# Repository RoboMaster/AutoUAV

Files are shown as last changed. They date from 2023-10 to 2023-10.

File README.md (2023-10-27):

# Robomaster自主无人机

## 注意
组装文档中采用了悬挂方案安装飞控，该方案能够极大地减小震动对imu的影响。但是长时间的拉伸会使得皮筋产生脆化而失去弹性。将皮筋更换为工业橡皮筋可缓解该问题。同时碳纤维板上预留了飞控安装孔位，也可以选择直接将飞控安装到碳板上，但是该做法的imu减震性能不佳。

## 简介
为了降低选手参与自主无人机赛事的门槛，减少用于调试安装设备的精力，推出了基于DJI Avata平台，Nvidia Jetson Xiaver NX 和 Ardupilot的开源自主无人机方案。  
*docs/RMUA2023自主无人机开源手册_bom.xlsx*包含有所需设备的详细信息，根据这个表格可以获得所需的所有零部件。  
*docs/RMUA2023自主无人机开源手册.md*详细介绍了安装，调试，参数配置，程序开发的全过程。按照该手册的指引，能够从0开始获得可以自主定位，手动或者离线控制的自主无人机。    
*models*中包含有所需的非标件模型文件。   
*catkin_ws_d430_ros*含有多个基本离线控制程序案例以供参考：
1. 视觉定位 (*catkin_ws_d430_ros/src/d430_slam*)；
2. 定点悬浮 (*catkin_ws_d430_ros/src/offboard*)；
3. 位置控制巡航 (*catkin_ws_d430_ros/src/offboard*)；
4. 速度控制巡航 (*catkin_ws_d430_ros/src/offboard*)；

## License
本项目使用*GNU GPLv3*，查看*LICENSE*文件获得更多信息。

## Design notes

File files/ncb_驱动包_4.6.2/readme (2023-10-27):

### NCB00 USB-OTG and TF socket driver setup

## FOR EMMC NX module
	// ON PC
	1, cp tegra194-p3668-all-p3509-0000-ncb.dtb ~/nvidia/nvidia_sdk/JetPack_4.6_Linux_JETSON_XAVIER_NX_TARGETS/Linux_for_Tegra/kernel/dtb/tegra194-p3668-all-p3509-0000.dtb
	2, Let NX/NANO enter recovery mode and connect to PC via micro-USB
	3, cd ~/nvidia/nvidia_sdk/JetPack_4.6_Linux_JETSON_XAVIER_NX_TARGETS/Linux_for_Tegra
	4, sudo ./flash.sh -r -k kernel-dtb p3449-0000+p3668-0001-qspi-emmc mmcblk0p1
	5, wait NX/NANO booting up.  

	// On NX
	1, cp extlinux.conf /boot/extlinux/ 
	2, reboot //important!!!

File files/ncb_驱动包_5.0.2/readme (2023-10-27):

### NCB00 USB-OTG and TF socket driver setup

## FOR EMMC NX module
	// ON NX
	1, sudo cp kernel_tegra194-p3668-0001-ncb00.dtb* /boot/dtb/
	2, sudo cp extlinux.conf /boot/extlinux/ 
	3, sudo reboot //important!!!
## USE TF card of NCB as rootfs
   1, Edit extlinux.conf to switch emmc and tf as rootfs  // ON emmc 
   2, ON TF card: cp extlinux-tf.conf /boot/extlinux/extlinux.conf //

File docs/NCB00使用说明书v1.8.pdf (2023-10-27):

未经同意，请勿转载全部或部分内容！

第 1 页 共 19 页

# NCB00 说明书

### 版本：v1.8

第 2 页 共 19 页

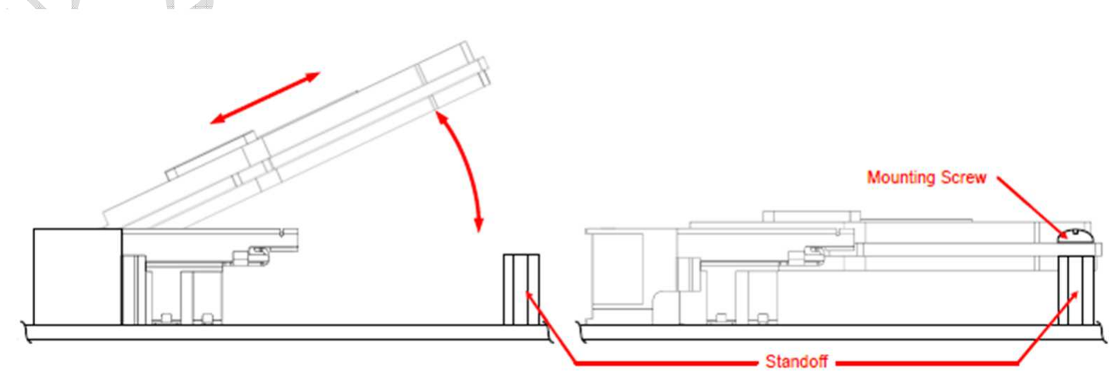
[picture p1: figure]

第 3 页 共 19 页

# 1. 版本历史

版本 | 修改说明 | 作者 | 备注
1.8 | 增加常见问题 | 张建军
1.7 | 完善 CSI 接口 I2C 说明，增加 USB2.0 说明 | 张建军
1.6 | 增加常见问题、IMU 等 | 张建军
1.5 | 针对 B07 更新 SPI 引脚定义说明 | 张建军
1.4 | 修正 NX GPIO 编号定义 | 张建军
1.3 | 添加 B05 版本说明 | 张建军
1.2 | 添加 B04 版本说明 | 张建军
1.1 | 添加 B03A 版本说明 | 张建军
1.0 | 新建 | 张建军

# 2. 安装方法

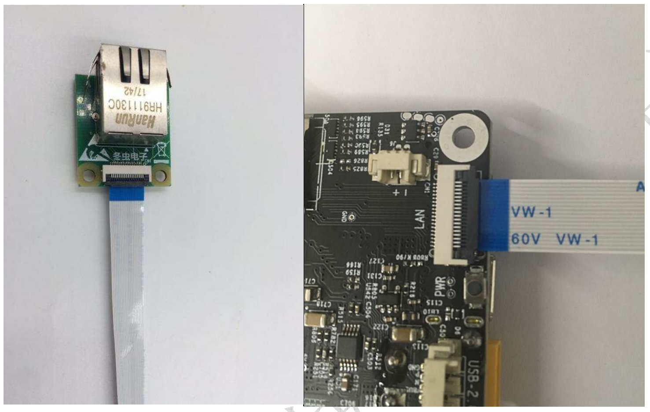
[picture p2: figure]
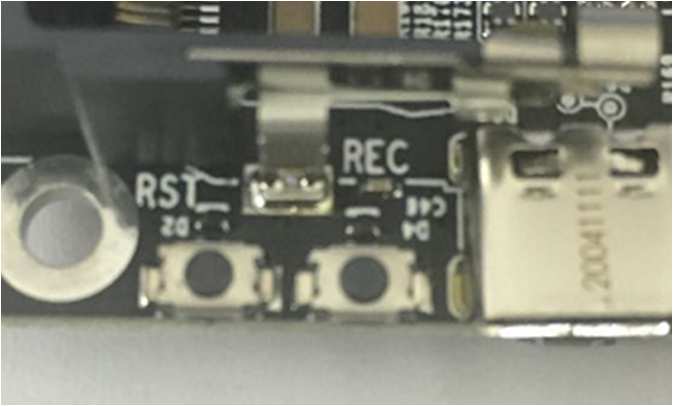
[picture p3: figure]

第 4 页 共 19 页

# 3. 配件连接

虽然板上配件接口大部分采用防呆防接反设计，但在连接时也必须在断电状态下进行， 并确认配件接到了相应的接口。
除特别说明外，配件的 FPC 接口连接方式都是相同的，均采用下接方式。如网口板的连 接照片

# 4. 如何刷机

1，刷机准备：准备一台 ubuntu18.04 以上系统的 PC，并安装 NVIDIA 最新版本的 sdkmanager。
2，进入 Recovery 模式：按住 REC（recovery）键，再按一下 RST（Reset）键，约 2 秒后 松开 REC 键，NANO/NX 进入 Recovery 模式，等待刷机。
3，刷机：通过 MicroUSB 线连接到 PC，并启动 sdkmanager，按提示步骤完成刷机。

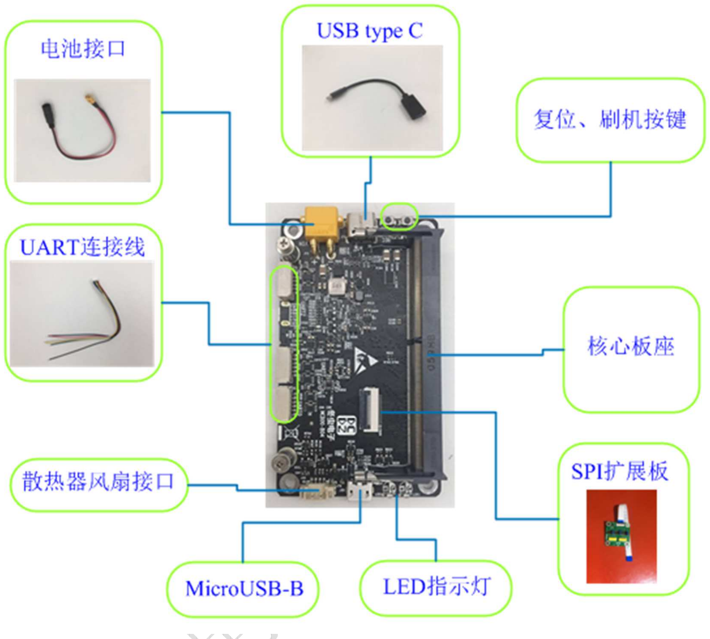
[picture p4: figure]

第 5 页 共 19 页

# 5. 接口说明

顶面视图

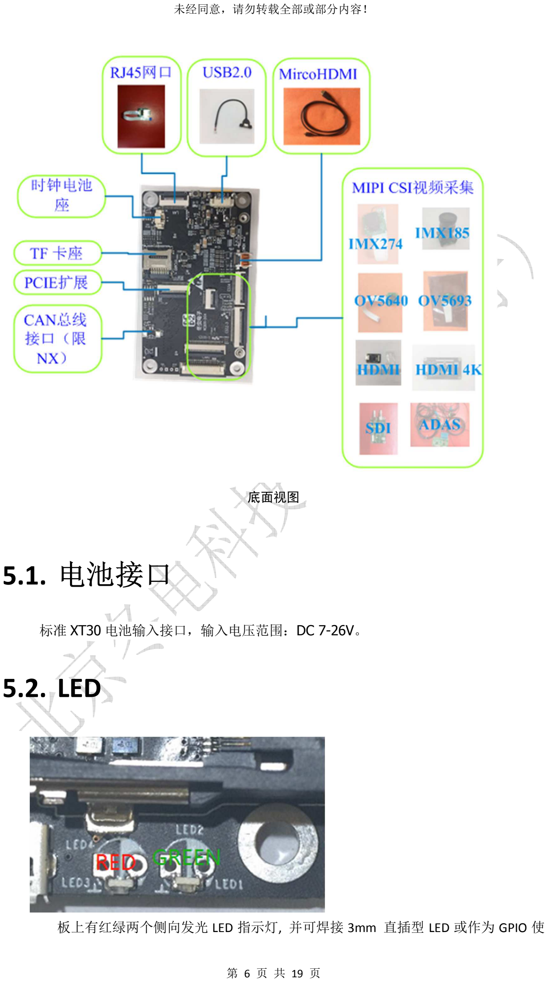
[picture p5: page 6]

第 6 页 共 19 页

底面视图

# 5.1. 电池接口

标准 XT30 电池输入接口，输入电压范围：DC 7-26V。

# 5.2. LED

板上有红绿两个侧向发光 LED 指示灯, 并可焊接 3mm 直插型 LED 或作为 GPIO 使

第 7 页 共 19 页

用。红色为底板电源指示灯，绿色为软件可控制的。
绿色 LED 控制信号为 GPIO12（开发板上的定义)，高电平时点亮。NANO 系统中对 应 GPIO 号为 194，NX 中为 268
Linux 系统中 IO 命令行调用方法：

echo "<number>" > /sys/class/gpio/export
echo "out" > /sys/class/gpio/gpio<number>/direction echo "0" > /sys/class/gpio/gpio<number>/value echo "1" > /sys/class/gpio/gpio<number>/value

# 5.3. MicroHDMI

HDMI type D 母座，HDMI 显示输出接口

# 5.4. UART0,UART1,UART2

UART0~1 为 4 线制 UART 接口，UART2 为 2 线制, 可把 UART 信号线配置为 GPIO 使用（需要修改驱动）。信号电平可选择为 5V 或 3.3V，出厂缺省为 3.3V 电平，采用 6pin 1.25mm 间距 GH1.25 带锁扣连接器。拔出时注意要按压解锁按钮。 UART0~UART2 与系统中对应关系如下表所示
UARTX | NANO | NX | 备注
UART0 | /dev/ ttyTHS2 | /dev/ ttyTHS1
UART1 | /dev/ ttyTHS1 | /dev/ ttyTHS0 | 系统占用（note）
UART2 | /dev/ttyS0 | /dev/ttyTCU0 | 系统占用（note）

note：在 NVIDIA 的官方系统中 UART1 和 UART2 默认为系统控制台，可按下面方法修 改为普通 UART 使用
UART1: 修改方法

### $ systemctl stop nvgetty $ systemctl disable nvgetty $ udevadm trigger $ sudo reboot UART2: 去除 cbootargs 和 extlinux.conf 中使用 ttyS0 的项

引脚定义如下图所示

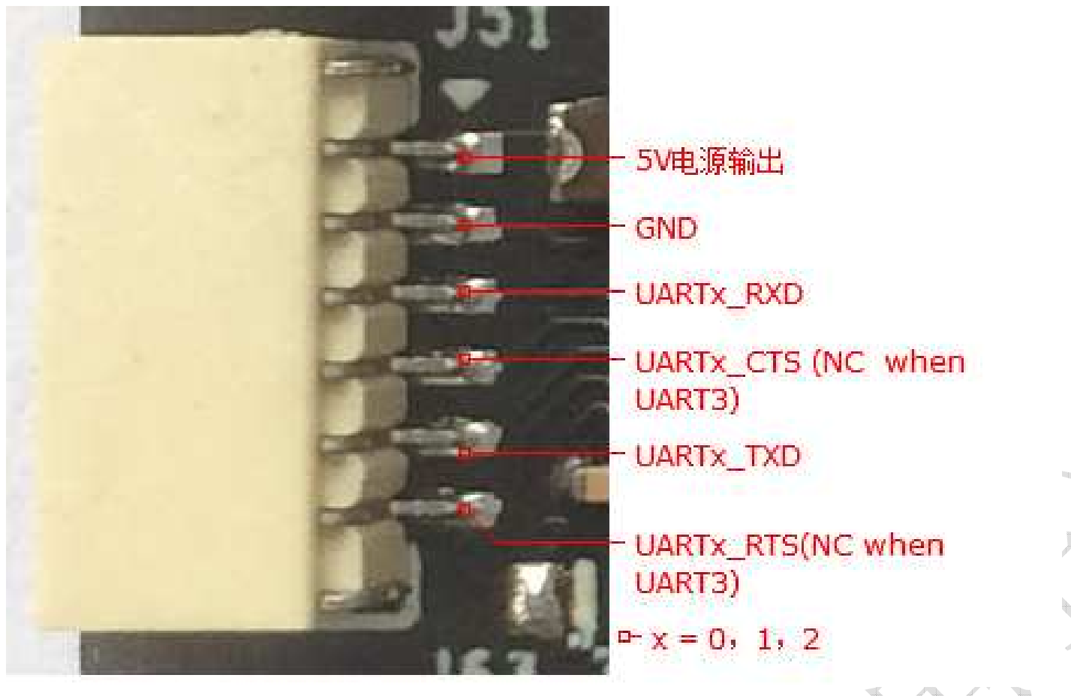
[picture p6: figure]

第 8 页 共 19 页

# 5.4.1. UART0

信号电平可通过接口附近的 R679 和 R678 进行选择，焊接 R679 时为 5V，焊接 R678 时为 3.3V，

# 5.4.2. UART1

信号电平可通过正面的 R681 和 R680 进行选择，焊接 R681 时为 5V，焊接 R680 时为 3.3V，

# 5.4.3. UART2

信号电平可通过正面的 R683 和 R682 进行选择，焊接 R683 时为 5V，焊接 R682 时为 3.3V，

# 5.5. IMU

板载 BMI160 IMU（可选项）, 地址为 7h69。使用 NANO 时 I2C 总线为 I2C1,测试命令： sudo i2cdetect –y –r 1；使用 NX 时 I2C 总线为 I2C8,测试命令：sudo i2cdetect –y –r 8

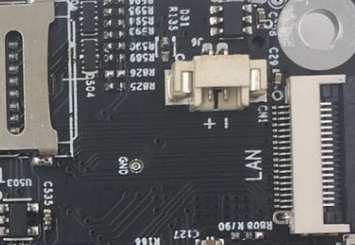
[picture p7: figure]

第 9 页 共 19 页

# 5.6. RTC 后备电池接口

采用 2pin MX1.25mm 座，官方系统默认支持 3V 的充电电池

# 5.7. Fan

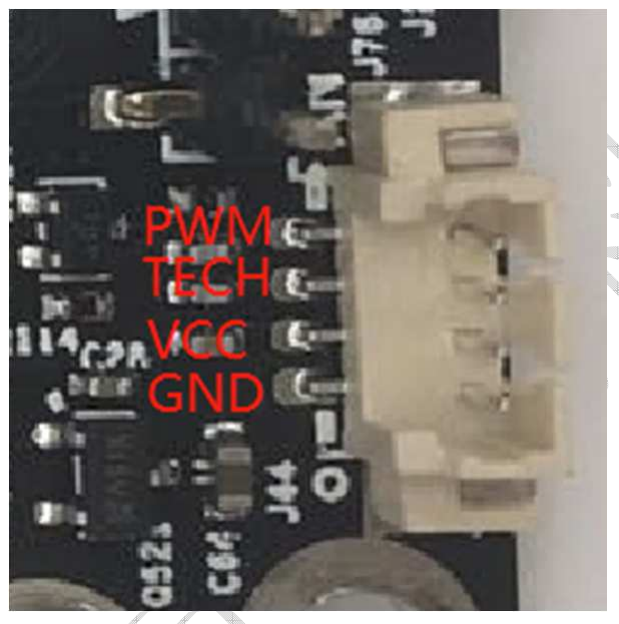
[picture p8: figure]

4pin MX1.25mm 连接器. 测试方法：
：sudo su
：echo 255 > /sys/devices/pwm-fan/target_pwm | //让风扇工作在最高速度

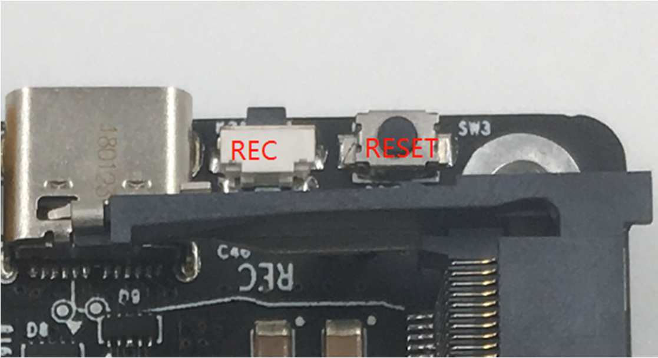
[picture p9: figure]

第 10 页 共 19 页

# 5.8. Key

电源开关键位于 USB type C 背面，其中 Recovery 键为侧向按键。默认为上电开机， 长按电源键超过 10 秒强制关机

# 5.9. USB 2.0 主机接口

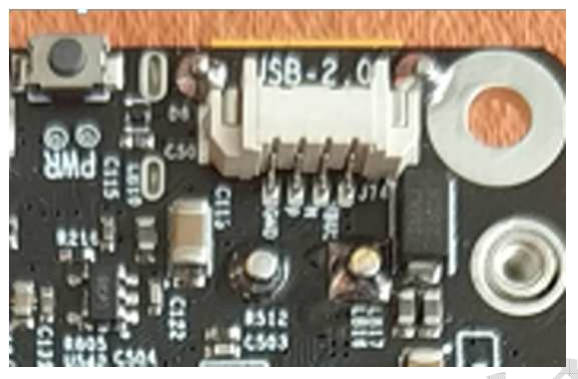
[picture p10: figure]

板载一个 USB2.0 主机接口，采用 4pin MX1.25mm 连接器

# 5.10. Micro USB

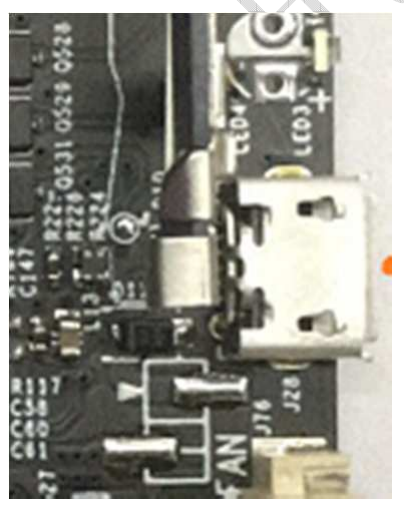
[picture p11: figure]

Micro USB B 座，支持 USB-0TG 功能（B05 以上版本），需要按驱动包中 readme 说明 更新 dtb 激活该功能

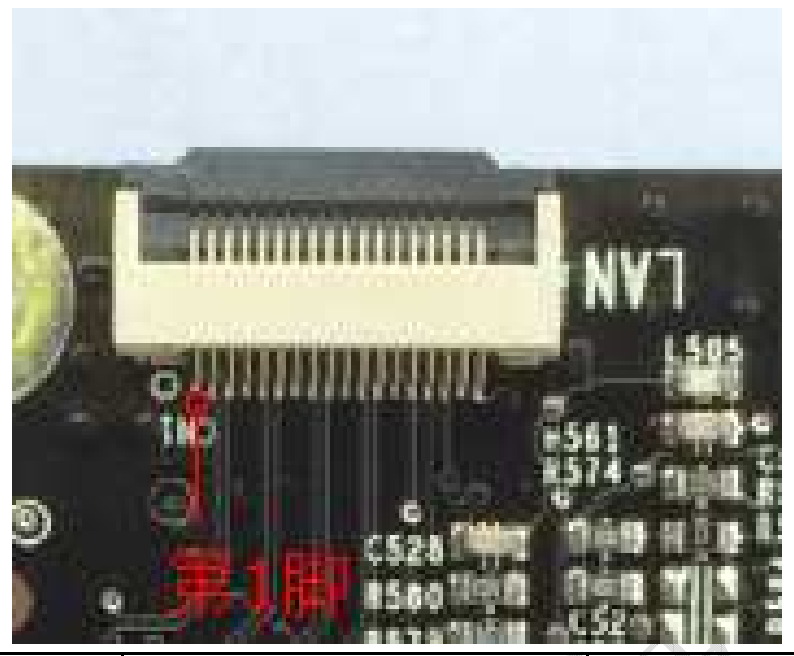
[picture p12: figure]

第 11 页 共 19 页

# 5.11. USB type C 座

标准 USB 3.0 是组合了 USB2.0 信号和 USB3.0 信号的接口，因为技术原因，在使用 USB2.0 设备时可支持任意方向插入，在使用 USB3.0 设备时请注意方向。USB 口电源 默认跟随 3.3V 电源打开，需要使用 GPIO 控制 USB 电源的请联系我司技术人员。

# 5.12. Gbe ethernet

千兆以太网扩展口,采用 18pin 0.5mm FFC 连接器。引脚定义如下所示

引号序号 | 信号名称 | 备注

1 GND
2 GBE_MDI0_N
3 GPE_MDI0_P
4 GND
5 GBE_MDI1_N
6 GBE_MDI1_P
7 GND
8 GBE_MDI2_N
9 GBE_MDI2_P
10 GND
11 GBE_MDI3_N
12 GBE_MDI3_P
13 GND
14 GBE_LED1
15 GBE_LED0
16 GBE_LED2
17 GND
18 | 3V3_SLP | 3.3V 电源输出

第 12 页 共 19 页

# 5.13. GPIO

提供 3 个输入和 3 个输出 IO，，分别位于 3 个 UART 接口。电平 3.3V 或 5V 可选，见 UART 接口电平配置方法，默认电平为 3.3V
系统 IO 编号见下表
UART 接口 | UART 引脚号 | 模组引脚名 | Jetson.GPI O 库 | NANO 系统 IO 号 | NX 系统 IO 号 | 备注
UART0 | 4 | UART0_CTS | -- | 28 | 479 | 输入
| 6 | UART0_RTS | -- | 27 | 478 | 输出
UART1 | 4 | UART1_CTS | 36 | 51 | 429 | 输入
| 6 | UART1_RTS | 11 | 50 | 428 | 输出
UART2 | 4 | GPIO11 | 31 | 200 | 422 | 输入
| 6 | GPIO07 | 32 | 168 | 424 | 输出

注：除了这几个 GPIO 外，LED 控制脚也可配置为 GPIO 使用。

# 5.14. Micro SD

翻盖式 Micro SD 卡座，需要按驱动包中 readme 说明更新 dtb 激活该功能。

# 5.15. EEPROM

板载 2k bit EEPROM, 地址为 7h57。使用 NANO 时 I2C 总线为 I2C2,测试命令：sudo i2cdetect –y –r 2；使用 NX 时 I2C 总线为 I2C0,测试命令：sudo i2cdetect –y –r 0

# 5.16. PCIe 扩展座

引出 PCIe x 1 接口，采用 22pin 0.5mm FFC 连接器，用来连接 miniPCIe 和 M.2 扩展板， 引脚定义如下图所示。

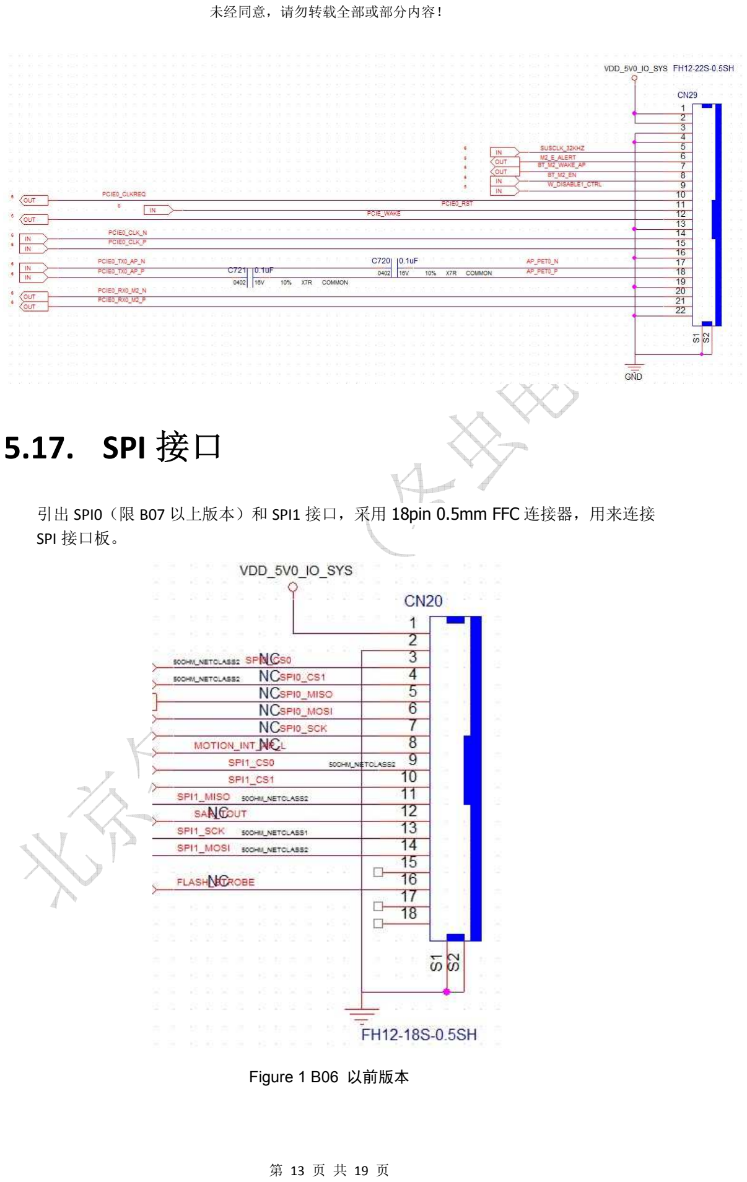
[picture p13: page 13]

第 13 页 共 19 页

# 5.17. SPI 接口

引出 SPI0（限 B07 以上版本）和 SPI1 接口，采用 18pin 0.5mm FFC 连接器，用来连接 SPI 接口板。

Figure 1 B06 以前版本

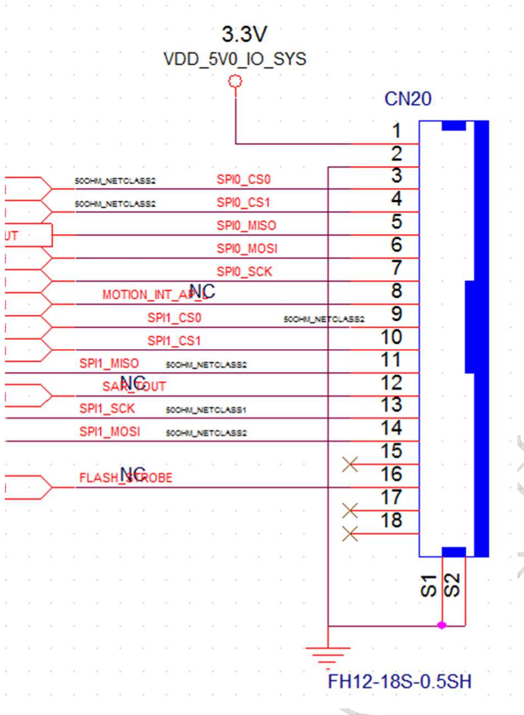
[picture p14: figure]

第 14 页 共 19 页

Figure 2 B07 以后版本

# 5.18. CSI-XX：

核心板的 CSI 信号分成 3 组引出，采用 30pin 和 22pin 0.5mm FFC 连接器。 CSI 接口 I2C 资源分配表
CSI 接口 | NANO | NX
I2C 总线地址 | I2C 设备节点 | I2C 总线地址 | I2C 设备节点
CAM0 | 0x546C0000 | /dev/i2c-6 | 0x3180000 | /dev/i2c-2
CSI0-1 | 同上 | 同上 | 同上 | 同上
CSI2-3 | 0x7000C400 | /dev/i2c-1 | 0x31e0000 | /dev/i2c-8
CSI4 | 0x7000C000 | /dev/i2c-0 | 0xc240000 | /dev/i2c-1

引脚定义如下所示

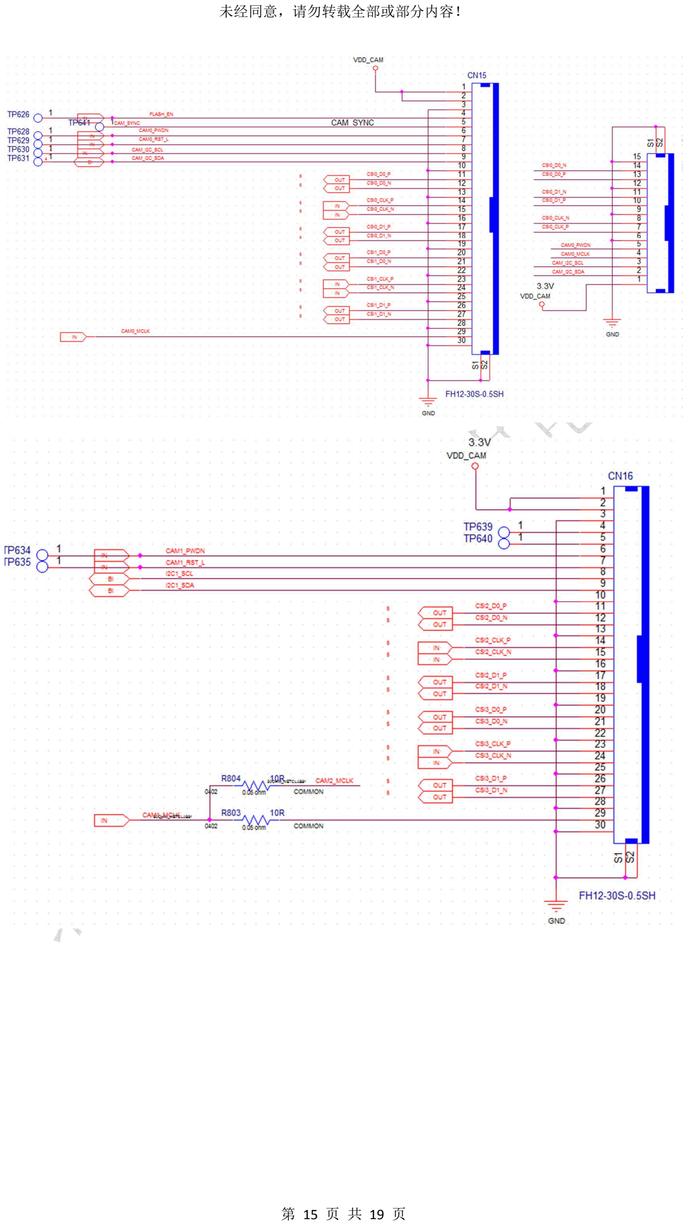
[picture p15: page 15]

第 15 页 共 19 页

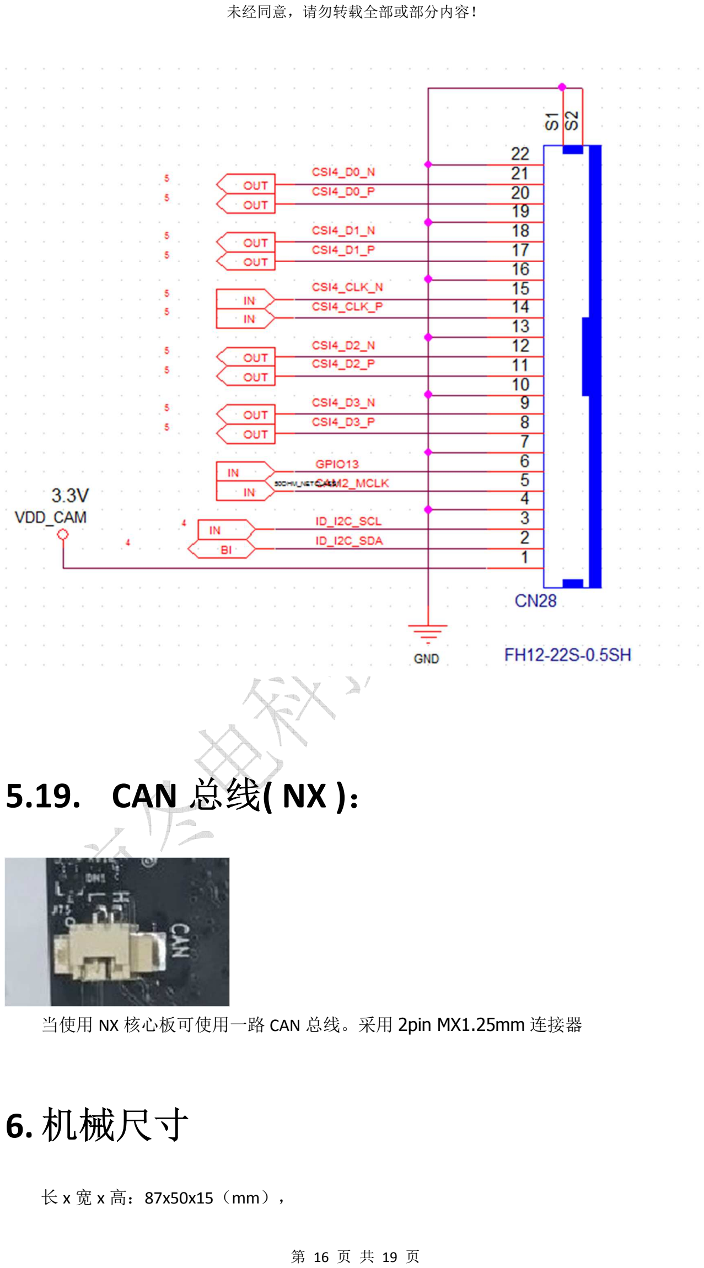
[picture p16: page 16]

第 16 页 共 19 页

# 5.19. CAN 总线( NX )：

当使用 NX 核心板可使用一路 CAN 总线。采用 2pin MX1.25mm 连接器

# 6. 机械尺寸

长 x 宽 x 高：87x50x15（mm），

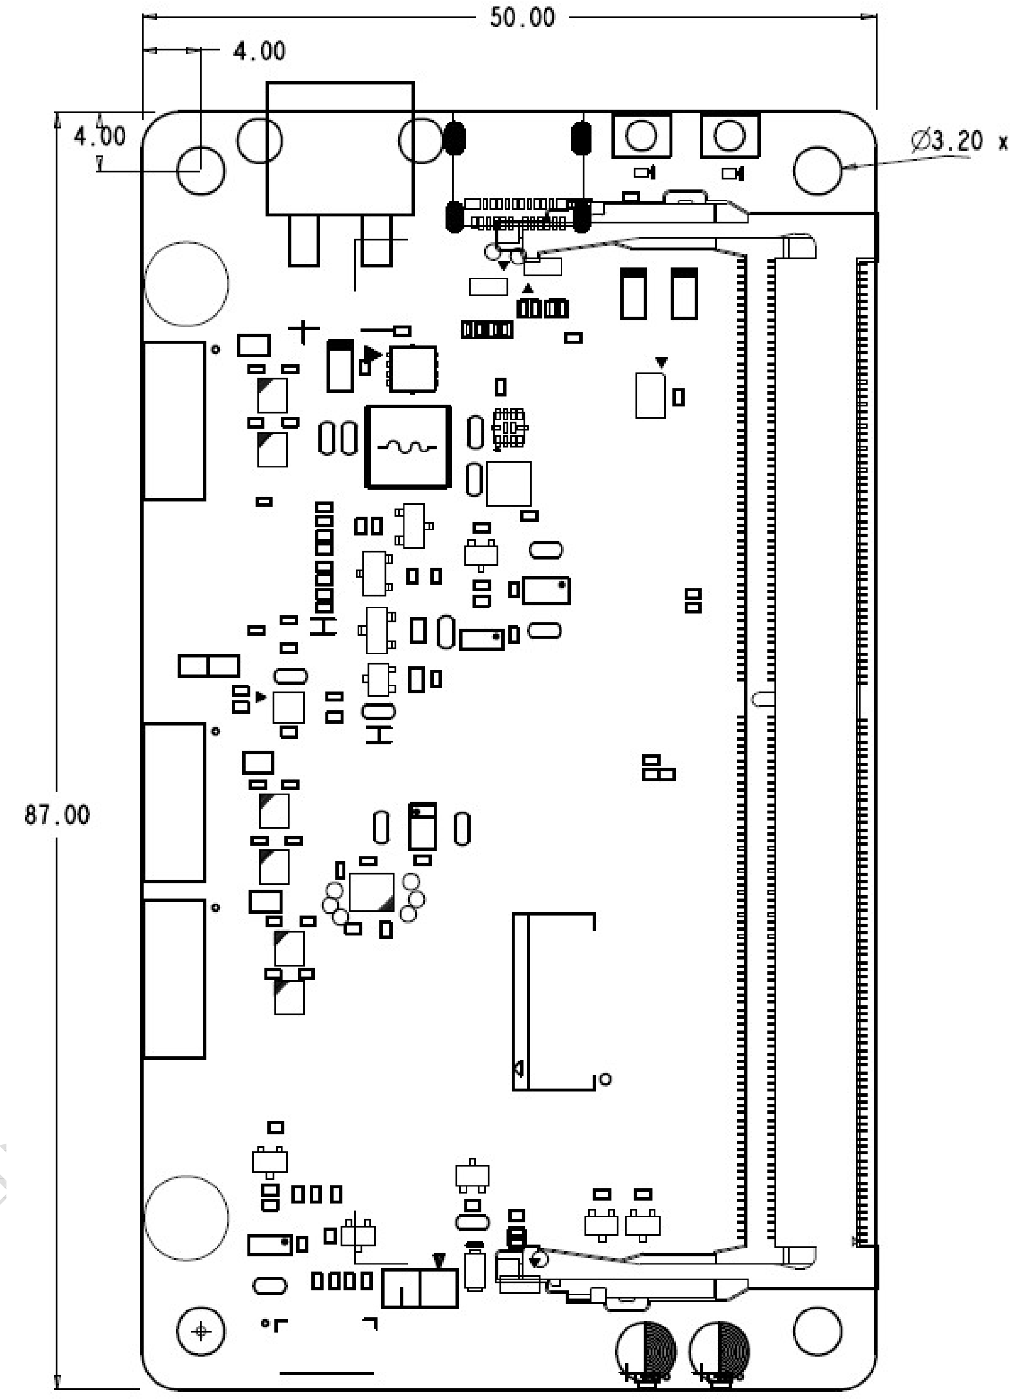
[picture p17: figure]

第 17 页 共 19 页

质量：30g

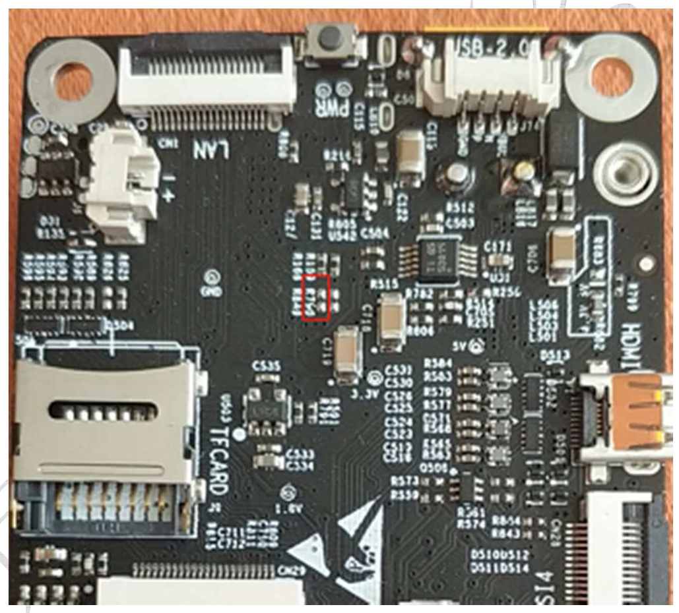
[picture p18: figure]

第 18 页 共 19 页

# 7. 配件列表

详 | 见 | 淘 | 宝

https://item.taobao.com/item.htm?spm=a2oq0.12575281.0.0.50111deb8W6Qks&ft=t&id=6139 84388047

# 8. 常见问题

### 8.1. Q1：连接 ZED 等 USB 设备时，自动启动时无法识别，手动插拔可以识别

A1：可以系统启动后通过关闭再打开 USB（type C 和 4pin USB 接口）电源来解决。 注：以下方法针对 NCB00-B07 及以上版本，其它版本请联系售后。
| NANO 系统中控制 USB 电源的 GPIO 号为 6，1 时打开 USB 电源，0 时关闭 USB
| 电源，注意该 GPIO 与 HDMI 共用，因此关闭 USB 电源时，HDMI 也会关闭
| NX 系统中需要焊接上电阻 R849（0402 封装，阻值建议 100R~1K），控制 USB
| 电源的 GPIO 号为 267，1 时打开 USB 电源，0 时关闭 USB 电源，系统启动时
| 默认 USB 电源为关闭状态。电阻位置如下图所示

Q2: 当使用 emmc 版本的 NANO/NX 模组时，如何使用 NCB 的板载 TF 卡作 rootfs A2：当使用 emmc 版本的 NANO/NX 模组时，可以使用 NCB 的板载 TF 卡作 rootfs。步骤 如下
| 按 NV 官方的方法烧写一个镜像到 TF 卡中。
| 按配套软件包说明激活 NCB 的板载 TF 卡。操作完成后，进入系统能自动识别
| 挂载 TF 卡，说明操作成功
| 然后参照下图修改 /boot/extlinux/extlinux.conf，并保存 reboot（不是断电重启）。

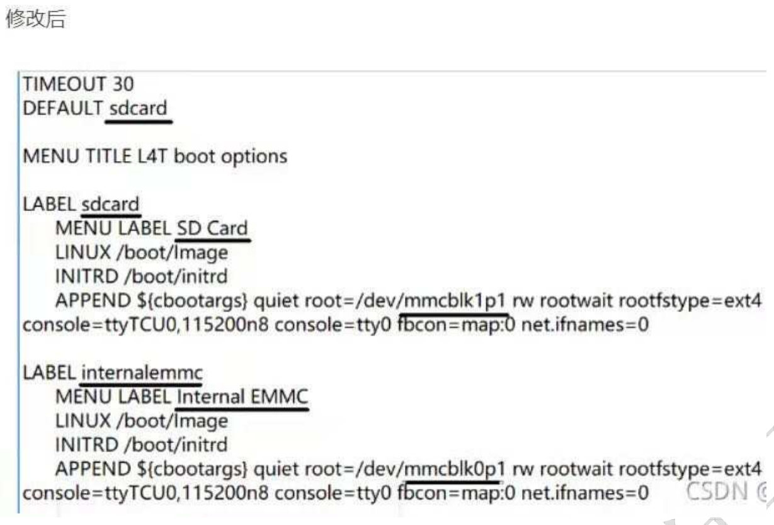
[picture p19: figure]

第 19 页 共 19 页

系统正常重启后会使用 TF 卡作为文件系统。

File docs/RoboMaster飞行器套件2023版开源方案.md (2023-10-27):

## 目录
---
>简述  
>版本   
>线路连接  
>Jetson NX配置  
>组装说明  
>飞控软件配置  
>遥控设置  
>第一次飞行  
>视觉定位   
>离线控制  
>高级  
>Q&A

## 简述
---
>基于DJI Avata机身与Ardupilot开源飞控设计的自主无人机平台开源方案。*boms.xlsx*文件提供了详细的物料信息，结合本文档可以制作出完整的自主飞行无人机平台。  
该无人机平台使用英伟达Jetson_NX为机载算力平台，Realsense D430为视觉模块，pixhawk2.4.8为飞控。本开源方案集成了视觉定位功能，可直接使用遥控定高，定点控制，或者基于ros离线控制无人机。 
本方案具有一定程度的抗撞击特性，经过18次各个面从3米高度自由落体到爬行垫上的测试后，无人机能正常进行定点飞行，测试过程参考 *docs/videos/撞击测试.mp4*

## 版本  
---
### V1.0

## 线路连接
---
    

> 线序说明参考 *docs/boms.xlsx*。  
>1. 电机-电调连接线，按图示顺序依次焊接即可。
>2. 电调-电流计连接线，需注意正负极。
>3. 电池-风扇-电流计并联线，若风扇转向相反，可手动调换风扇2pin接口线序。  
 
>4. 电流计-记载电脑电源线，焊接时需注意正负极。
>5. 电流计-飞控电源线，直接连接即可，两端无区别。  
  
>6. 飞控-Jetson NX串口线, GH端口（下边）接入Jetson NX UART1(中间的串口)，JST端口（上边）接入飞控TELEM1或者TELEM2。  
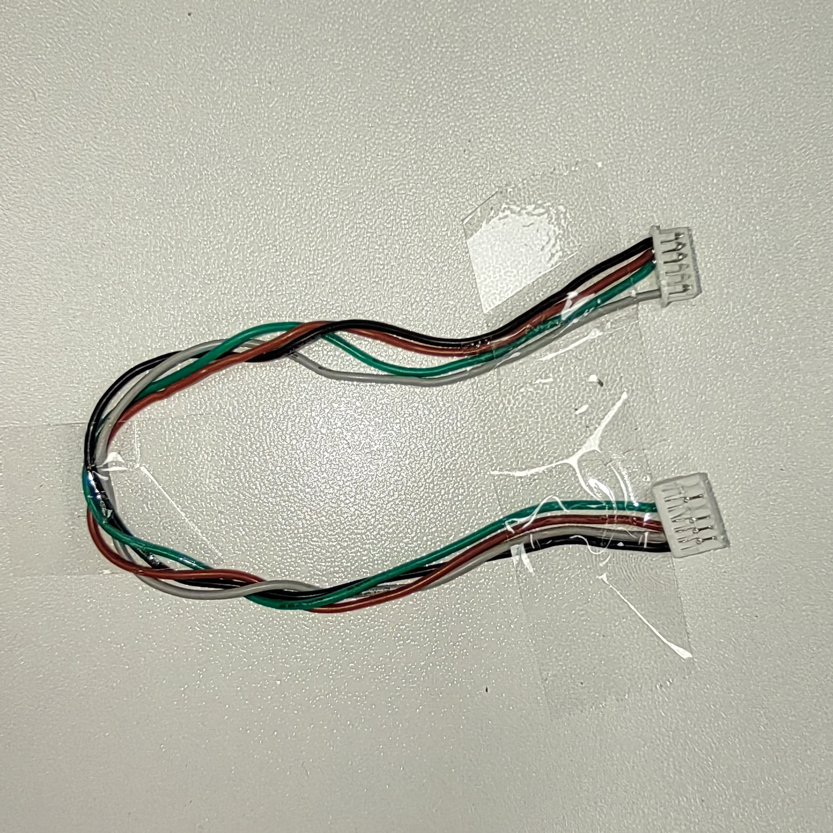
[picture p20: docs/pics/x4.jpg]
  
>7. 电机信号线，下图一为电调端接口，除了红黑线外，其余线对应电调上的1~4号电机标识。下图二为飞控上的引脚定义，蓝色为可用电机线号接口，红色是正极，黑色是负极。电机线号线的红黑色线必须接到对应颜色的飞控端口，其余四根线可随意接在蓝色任意端口。  
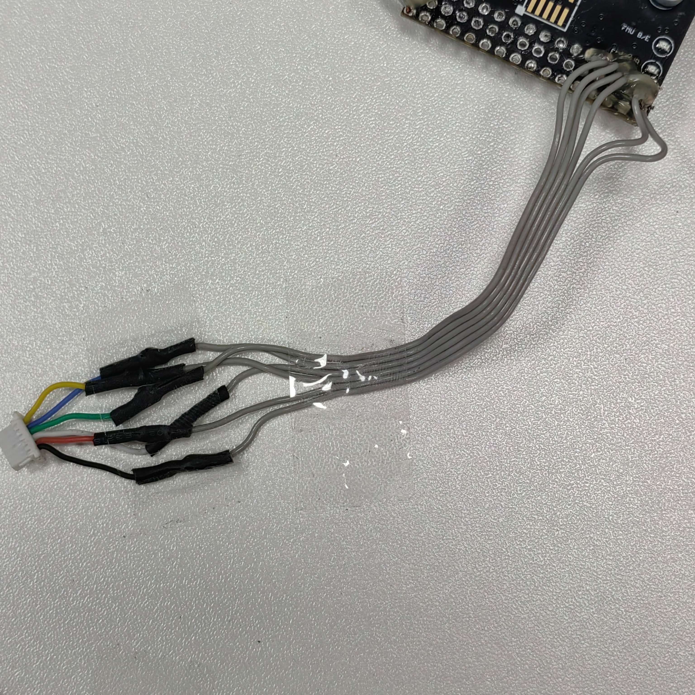
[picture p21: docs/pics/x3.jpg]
 
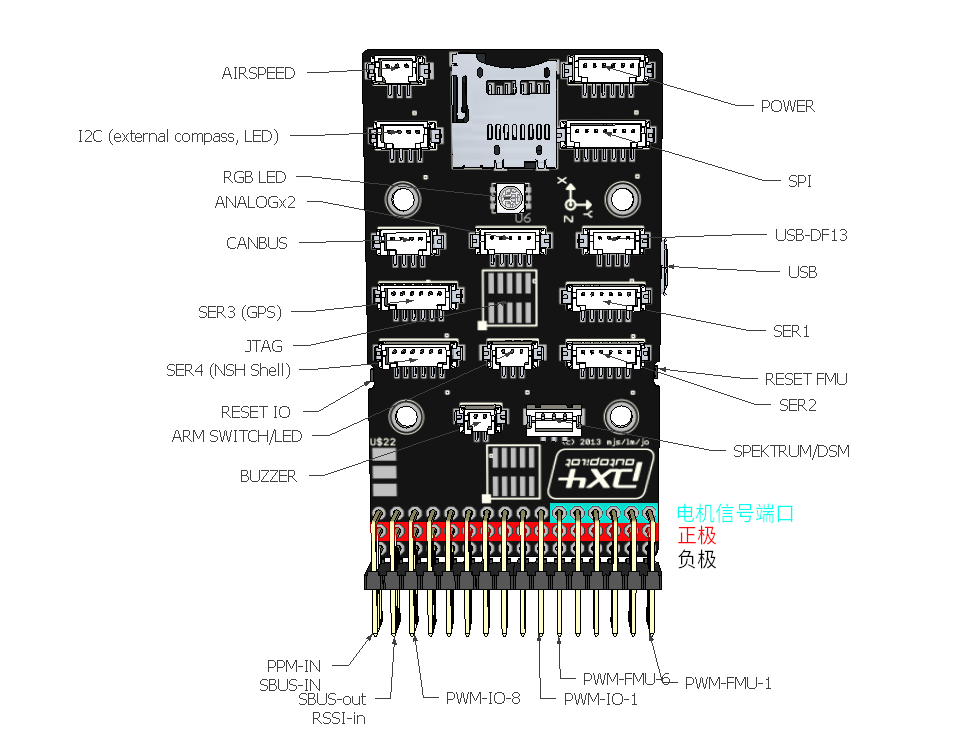
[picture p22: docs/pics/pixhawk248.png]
  
>8. FPC软排线type-c数据线。  
>9. 接收器连接线。  
    
>10. usb wifi 模块转接线。  
 

## Jetson NX配置
---
### 使用SDK Manager刷写系统
>Jetson NX需要先使用官方的*SDK Manager*软件刷系统进入EMMC中，确认EMMC系统工作之后才能在SD卡刷系统。载板使用参考*docs/NCB00使用说明书v1.8.pdf*。  
>1. 首先在*UBUNTU 20.04*中下载*SDK Manager*，地址为 *https://developer.nvidia.com/sdkmanager_deb*。安装成功后，打开软件，使用开发者账户登录。  
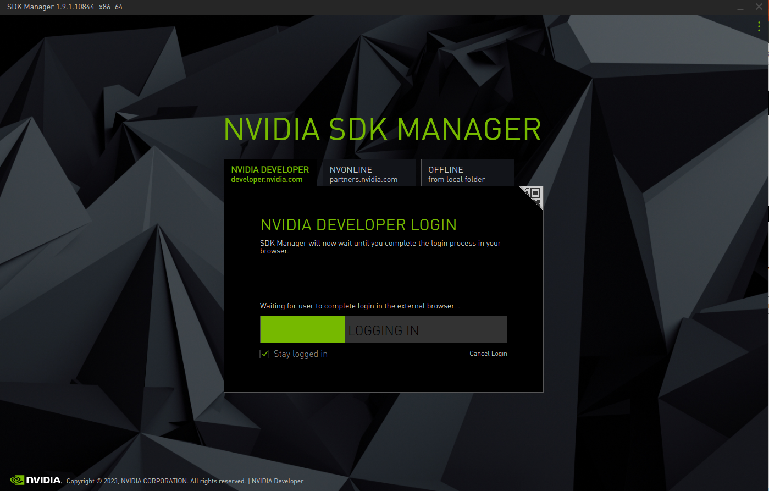
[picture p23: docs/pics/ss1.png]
>
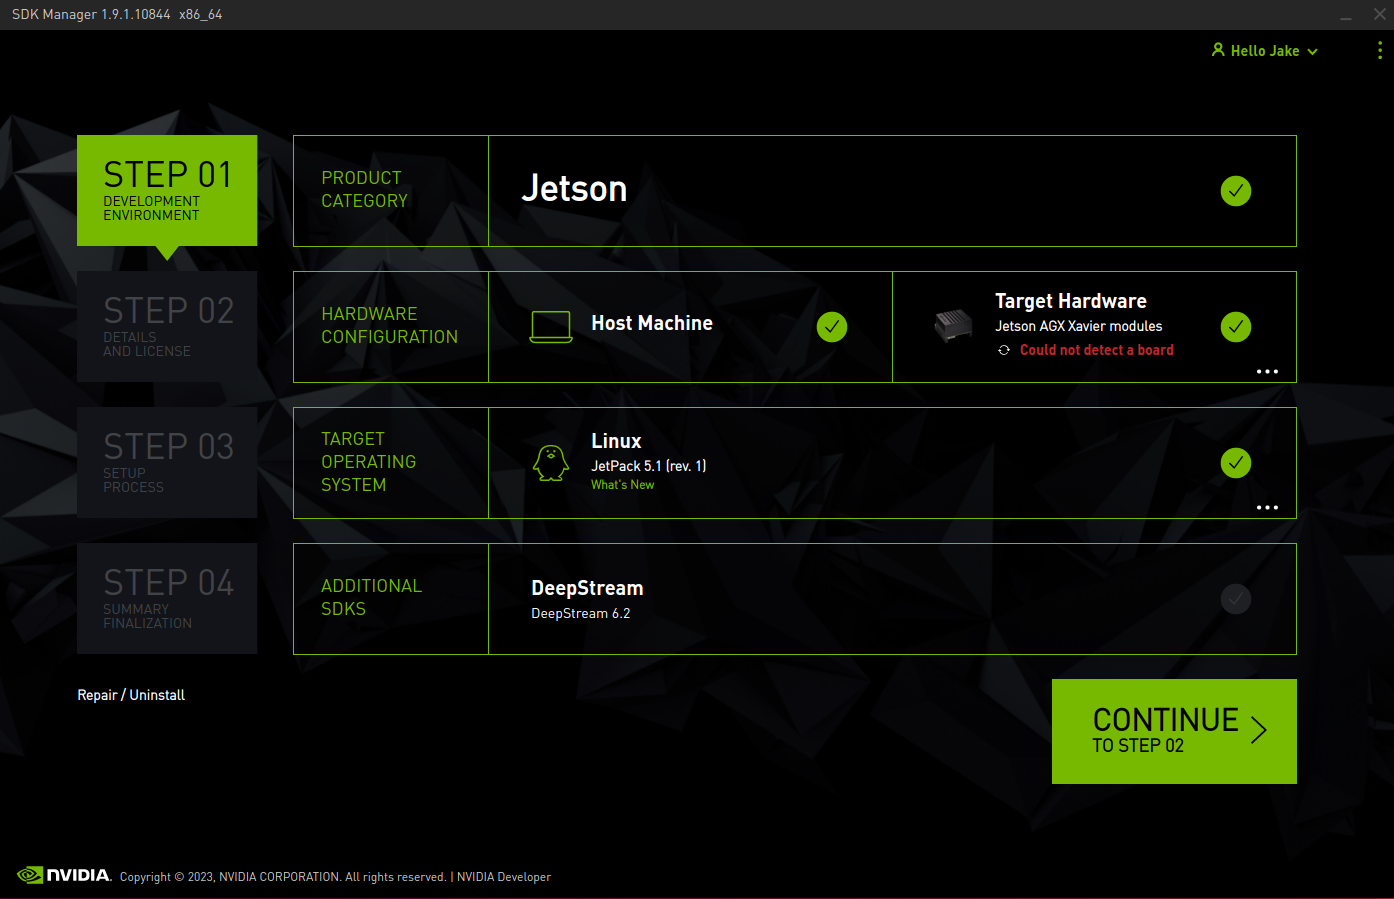
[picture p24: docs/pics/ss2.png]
>    
>2. 给Jetson NX接入电源，红色电源指示灯亮起。在type c接口旁边有两个按键，分别是*REC*,*RST*。按住*REC*两秒后，按一下*RST*，接着松开*REC*。当红色指示灯变暗时（不是熄灭），说明Jetson NX进入了刷机模式。此时会提示检测到硬件，选择第一项。  
>  
>3. 在操作系统中选择*Jetpack 5.0.2*，取消勾选*Deepstream*。点击*Continue*。  
> 
>4. *Target Components*为可选项，可以在这里一起安装或者之后自行安装。勾选*I accept ....* 后，点击*Continue*。  
> 
>5. 如果提示文件夹不存在要创建之类的问题，点击确认。按提示输入管理员密码后，进入刷机流程，等待即可。  
> 
>6. 下载完毕之后出现如下页。选择*Manaual Setup-Jetson Xavier NX*。7处选择*Pre-Config*,下方输入要使用的用户名和密码，这里用了默认的*nvidia*作为账户密码。此时连接显示器和键盘鼠标到NX上，方便查看刷写进度，然后点击*Falsh*后等待。再接近完成时，NX会自动从刷机模式退出进入系统，显示屏中会出现系统开机画面。继续等待直到*SDK Manager*提示*Installation Completed Successfully*。  
> 
>7. 点击*Finish*退出程序。  
> 
>备注：使用sd卡作为系统启动盘请参考 *files/ncb_驱动包_5.0.2/readme* 和 *docs/NCB00使用说明书v1.8.pdf*。

### 远程连接方案
>1. 准备一台路由器，使用网线连接主机与该路由器的LAN口。进入它的配置页面，在LAN配置中设置静态IP地址，这里分配的是 *192.168.100.1*，子网掩码是 *255.255.255.0*。  
>
>2. 设置无线网络。  
>
>3. 使用usb2.0转接线连接wifiusb模块到NX中。  
>
>4. 在NX中找到所配置的无线网络并连接。
>>Jetpack5中使用usb wifi 模块需要安装驱动。首先使用网线接口把NX联网，然后执行指令   
`sudo ubuntu-drivers autoinstall`  
`sudo apt update`  
`sudo apt install build-essential dkms gcc git make`  
`git clone https://github.com/brektrou/rtl8821CU.git`  
`cd rtl8821CU/`   
`chmod +x dkms-install.sh`  
`sudo ./dkms-install.sh`  
`sudo modprobe 8821cu`    
完成之后重启NX, wifi模块能够识别，选择相应的无线网络连接即可。  
>5. 在静态地址分配中找到NX的MAC地址并分配一个静态网址给它，这样当NX用wifi接入路由器后所得到的地址就不会变，方便后续ssh远程连接。
>    
>6. 使用ssh远程连接NX。  
>   

## 组装说明
---
>1. 把4颗M3.0\*10铝合金螺丝，4颗M3.0\*15尼龙柱，4颗4\*2.7\*2.5黑色ABS隔离柱与飞控固定板组装在一起。  
>
>
>  
>2. 使用2颗M3.0\*16铝合金螺丝与2颗M3.0防松螺母将电池固定架在飞控固定板上。  
>
>  
>3. 将两个黑色皮筋放到尼龙柱的底部。  
>
>  
>4. 把4颗M3.0\*10铝合金螺丝，4颗M3.0防松螺母和8颗4\*2.7\*2.5ABS黑色隔离柱与飞控按图示组装在一起。  
>
>    
>5. 按图示把黑色皮筋挂到飞控上。   
>
>  
>6. 使用尼龙扎带，风扇固定板把机载电脑与散热模块组装在一起，散热模块与NX核心模块之间需要涂导热硅脂。     
>
>
>  
>7. 按图示把2个皮筋挂到飞控的螺丝和尼龙柱上后，使用2颗M3.0\*25铝合金螺丝，2颗M3.0\*35铝合金螺丝和4颗4\*2.7\*2.5ABS黑色隔离柱把侧边防护固定件，机载电脑和飞控固定在一起。隔离柱处于机载电脑的下方。在组装时要使用钳子固定住下方尼龙柱，防止其旋转拉扯到皮筋。  
>
>  
>8. 如图将上一步中飞控上方挂到尼龙柱的皮筋用螺丝刀提到隔离柱的位置上，完成后飞控的姿态应当保持居中水平不与结构件发生碰撞。    
>
>  
>9. 使用2颗M1.4\*5螺丝把相机镜头与相机固定件连接后，使用3mm厚度3M双面海绵胶带把镜头与PCB板固定。    
>
>  
>10. 把usb wifi连接线装到载板上。  
>  
>11. 使用2颗M3.0\*5平头螺丝将相机模块固定到飞控固定板上。  
>
>
>
>12. 使用12颗M2.0\*5螺丝将电机按图示顺序固定到底板上。   
>
>  
>13. 把飞控电源线穿过底板中间孔位后接入电调中。  
>    
>14. 使用美工刀将图示红色框中的部分削平。  
>  
>15. 把4颗M2.5\*16螺丝与4颗M3.0\*5尼龙柱按图示固定到底板上,然后把电机信号线通过图示孔位穿过底板。    
>
>
>16. 如图使用4颗M2.5防松螺母把上下部分组装在一起。   
>  
>17. 把电机信号线接入电调中，然后使用电工胶带把电流计包裹住以防止短路，接着使用扎带把电调、电流计等固定好。  
>
>  
>18. 把NX电源线通过图示孔位穿过涵道圈。     
>    
>19. 使用4颗M2.0\*4螺丝将底板和涵道圈固定在一起。  
>
>  
>  
>20. 把NX电源线接入NX中，把串口线接入飞控TELEM1或者TELEM2和NX UART1中(串口线建议从飞控上方穿过)。同时把风扇线固定好。  
>
>  
>
>  
>21. 使用2颗M3.0防松螺母，4颗M3.0\*16铝合金螺丝，2颗M3.0\*10铝合金螺丝和2颗M3.0\*35尼龙柱把2个侧边防护板固定到机身上。  
>
>  
>22. 使用8颗M2.0\*6螺丝将桨叶固定到电机上，注意图示中不同桨叶的区别（是否带有黄点）。  
>
>  
>23. 使用6颗M2.0*4螺丝将加强件固定到涵道圈上。  
>
>
>24. 使用扎带把usb wifi模块，NX电源线，风扇线等固定好，其中wifi模块要按照图示放置以减少对进气的干扰。  
>
>  
>
>  
>25. 通电后效果。  
>
>  
>
>  
>
>

## 飞控软件配置
---
### mission planner
mission planner 是ardupilot的地面站控制软件，参考 *https://ardupilot.org/planner/docs/mission-planner-installation.html#mission-planner-on-linux* 进行安装。 

### 安装固件
>1. 使用micro usb 连接电脑与pixhawk2.4.8。
>2. 依次点击 *初始设置*，*安装固件 Legacy*，*加载自定义固件*。
  
>3. 选择 *arducopter 4.3.3_pixhawk.apj*，等待直到显示 *upload done*。
  

### 加载默认参数配置
>1. 使用micro usb 连接电脑与pixhawk2.4.8后，在右上角的端口下拉框中找到飞控对应的端口，右边的数字为串口波特率，选择*115200*，然后点击连接。最右上角的插头标识变为绿色说明连接成功。
>2. 依次点击 *配置/调试*，*全部参数*，*加载*。
  
>3. 选择 *ardupilot4.0_0329_fmuv3.param*，然后点击写入参数。显示 *Parameters successfully saved* 说明写入成功。  
    

## 遥控设置  
---
### 固件更新
>遥控器与接收机有各自的固件需要更新。本文档测试时，遥控器固件版本为2.3.15，接收机版本为2.1.6。遥控器与接受机的版本均分为国际版和欧洲版，两者必须同为欧洲版或同为国际版才能对频。  
遥控固件更新教程：*https://oscarliang.com/flash-opentx-firmware-taranis/#Download-OpenTX-Companion* ，同级文件目录中的 *Frisky遥控器固件* 为文档中所使用的遥控器固件。  
接收器固件更新教程：*https://oscarliang.com/flash-frsky-rx-firmware/*  
参考视频教程：*https://www.bilibili.com/video/BV1rf4y1k7G4/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*
### 遥控器模型配置
>1. 在 *http://www.open-tx.org/2022/04/22/opentx-2.3.15* 中根据使用的操作系统下载相应软件，这里使用Linux版本软件。
>2. 安装并打开软件。
  
>3. 如图，同时按这三个按键，使遥控器进入*bootloader*，然后使用usb线接入电脑。

>4. 点击*文件*， *打开*，选择*遥控器配置.otx*后出现*aa_a*模型配置。

>5. 点击左侧图标*将模型和配置写入遥控器*，等待写入完成。
### 接收机配对
>参考视频教程（30分53秒处）：*https://www.bilibili.com/video/BV1rf4y1k7G4/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*   
>配对完成后，给无人机和遥控上电，看到接收器led灯由红色转绿色，遥控器屏幕中出现信号图标说明已经进入工作状态。  
>
>  

### 遥控器校准
>依次点击*初始设置*，*必要硬件*，*遥控器校准*，*校准遥控*后，两次弹出框点击*ok*。
  
>此时绿色柱中会出现红色标识，将两个摇杆以及所有按键/旋钮推到极限位置，当绿色柱子呈现如图所示的状态时，点击*完成时点击*按钮即可。
>依次点击*初始设置*，*必要硬件*，*遥控器校准*，*校准遥控*后，两次弹出框点击*ok*。
  
### 摇杆功能
  

>遥控器的各个摇杆都是一个独立的输入源，这个输入源可以在遥控器中分配到不同的信道中。在飞控的参数配置中把信道跟不同的功能（如模式切换，横滚，俯仰，偏航，油门等）绑定在一起。由此，遥控与无人机就通过信道联系起来了。如下为默认配置文件中的摇杆功能分配。  
J1: 信道1，横滚。  
J2: 信道3，油门。  
J3: 信道2，俯仰。  
J4: 信道4，偏航。  
SG: 信道5，模式切换（max:自稳，center:定高，min:定点）。  
SH: 信道7，降落。  

## 第一次飞行
---
### IMU校准
>打开*Mission Planner*， 连接无人机后，点击 *初始设置* *必要硬件* *加速度计校准*。根据提示依次完成三项校准操作。
>    
### 电机校准
>1. 电机序号和转向在 *初始设置* *可选硬件* *点击测试* 中可以进行测试。
>  
>2. 把无人机的桨叶卸下来之后，依次点击 *Test Motor A* *Test Motor B* *Test Motor C* *Test Motor D* ,可以看到点击会分别转动。转动方向和序号应当符合下图所示。
>   
>3. 点击的序号和转动方向可以在 *初始设置* *必要硬件* *Servo Output* 中设置。 9-14号端口就是安装线路连接部分中展示的，电机线号线与飞控板连接6个可用端口。 勾选 *Reverse* 可更改相应电机的转动方向。
>  
### 手动自稳模式飞行
>完成上所述步骤，将桨叶安装好，重启无人机，启动遥控器后，把SG往上打切换到自稳模式，内八字打杆启动无人机，开始第一次飞行。

## 视觉定位
---
### Realsense驱动安装
>1. 断开相机连接，用SSH连接NX后，在NX中执行指令。  
>2. `git clone https://github.com/IntelRealSense/librealsense.git`  
>3. `sudo apt-get install curl git libssl-dev libusb-1.0-0-dev libudev-dev pkg-config libgtk-3-dev libglfw3-dev libgl1-mesa-dev libglu1-mesa-dev at apriltag`  
>4. `cd librealsense && sudo ./scripts/setup_udev_rules.sh`  
>5. `mkdir build && cd build`    
>6. `cmake .. -DCMAKE_BUILD_TYPE=Release -DBUILD_EXAMPLES=true`     
>7. `sudo make uninstall && make clean && make && sudo make install`  
>8. 连接相机后执行   `rs-hello-realsense`   
>9. 此时终端显示当前探测到的物体的距离，说明相机已经正常工作。
>  

### 安装ros
>1. `sudo sh -c 'echo "deb http://packages.ros.org/ros/ubuntu $(lsb_release -sc) main" > /etc/apt/sources.list.d/ros-latest.list'`  
>2. `curl -s https://raw.githubusercontent.com/ros/rosdistro/master/ros.asc | sudo apt-key add -`    
>3. `sudo apt update`  
>4. `sudo apt install ros-noetic-desktop python3-catkin-tools`  

### 安装opencv
>1. `git clone https://github.com/opencv/opencv.git --branch 4.2.0`  
>2. `cd opencv && mkdir build && cd build && cmake .. -DCMAKE_BUILD_TYPE=Release && make -j 6`  
>3. `sudo make install`  
>4. `sudo ldconfig`  

### 安装ORBSLAM3
>1. `cd ~ && git clone --recursive https://github.com/stevenlovegrove/Pangolin.git --branch v0.5`  
>2. `sudo apt install libglew-dev`  
>3. `cd Pangolin && mkdir build && cd build && cmake .. && make`    
>4. `cd ~ && git clone https://github.com/UZ-SLAMLab/ORB_SLAM3.git --branch v1.0-release`  
>5. `cd ORB_SLAM3`  
>6. 在*CMakeLists.txt*中按图示修改编译器版本，注意*add_definitions*参数不能改。
>   
>7. 在*CMakeLists.txt*中指定Pangolin的package路径，例如把*find_package(Pangolin REQUIRED)*修改为*find_package(Pangolin REQUIRED PATHS /home/nvidia/Softwares/Pangolin/build)*。
>   
>8. 在*CMakeLists.txt*和*Thirdparty/DBoW2/CmakeLists.txt*中指定*opencv*版本。  
>  
>9. `./build.sh #若编译过程中出现系统卡死的现象，参考最后一章Q&A第一节`   

### 编译功能包
>1. 把*catkin_ws_d430_ros* 文件夹拷贝到NX中。然后在NX的终端中，进入*catkin_ws_d430_ros*目录。   
>    
>2. `source /opt/ros/noetic/setup.bash`     
>3. 在*src/d430_slam/CMakeLists.txt*文件中，如图修改*orbslam*路径,该路径是*ORBSLAM3*的文件目录,不是*build*目录。  
>   
>4. 修改*src/d430_slam/src/node/orbslam.cpp*文件中，图示两个路径。第一个是*ORBSLAM3*的*ORBvoc.txt*所在路径，第二个是*settings.yaml*所在路径。  
>
>5. 安装依赖。`sudo apt install ros-noetic-mavros*`   
>6. 开始编译。`catkin build d430_slam apm_d430_bridge`    
>7. `sudo /opt/ros/noetic/lib/mavros/install_geographiclib_datasets.sh`     
>8. 启动视觉定位功能和远程通信功能。 `roslaunch d430_slam apm_d430_slam.launch`  

### 手动定点飞行
飞行效果参考： *docs/videos/手动定点飞行.mp4*。  
>1. 接着上一步，打开*MissionPlanner*，右上角选择*UDPCI*模式后点击连接。     
>  
>2. 在弹出框输入NX网络地址和*14550*端口号。  
>
>   
>3. 连接完成后无人机各项数据会显示在界面中。  
>   
>4. 使用遥控器切换飞行模式到*Loiter*, 窗口右下角会显示切换到的飞行模式。  
>  
>5. 使用遥控器油门控制，无人机会直线上升。油门居中后，无人机会定点悬停。  

## 离线控制
---
### 案例使用
飞行效果参考： *docs/videos/离线控制悬浮.mp4*，*docs/videos/离线控制位置控制巡航.mp4*，*docs/videos/离线控制速度控制巡航.mp4*。  
>在*catkin_ws_d430_ros/src/offboard*中完成了三个基本控制样例，分别实现了定点悬浮，位置控制巡航和速度控制巡航。通过在*offboard_test_node.cpp*中注释的方式激活特定案例。巡航案例中使用的均为简单的PID走航点模式，轨迹跟踪效果一般，仅供参考。    
>  
>1. 在NX中，进入*catkin_ws_d430_ros*文件夹中，编译样例。  
`catkin build offboard`  
>2. 启动定位功能与远程通信通能后并连接*MissionPlanner*，使用脚本设置原点。  
`pip3 install pymavlink`  
`python set_origin.py`  
>3. 完成后，会显示一台无人机在界面上，并且下方的高度会变成0.0m。  
>  
>4. 启动程序。  
`source devel/setup.bash && rosrun offboard offboard_test_node`  

### 无人机开发
完成上述步骤后，即可通过订阅主题的方式获得无人机的数据，并通过给特定主题发布数据来控制无人机。  

#### 可订阅主题（部分）
>slam原始数据： `/d430_camera/pose`   
>电池剩余电量： `/mavros/battery`  
>设置的世界坐标原点经纬度信息： `/mavros/home_position/home`  
>imu数据： `/mavros/imu/data_raw`  
>导航数据： `/mavros/local_position/odom`  
>姿态数据： `/mavros/local_position/pose`  
>无人机运行状态： `/mavros/state`  

#### 控制指令
通过给 `mavros/setpoint_raw/local` 主题发布数据即可完成位置控制，速度控制，姿态控制和角速度推力控制等。该主题数据类型为 `mavros_msgs/PositionTarget`，具体使用参考程序案例以及官方页面:   *http://docs.ros.org/en/api/mavros_msgs/html/msg/PositionTarget.html*。  
要注意的是，官方说明中参考坐标系是*NED/FRD*,但是实际使用中发现无人机还是按照*FLU*进行运动。

## 高级
---
### 外部定位数据
通过往 `/mavros/vision/pose` 或者 `/mavros/odometry/out` 中发布位姿信息即可完成，本案例中仅有位置和姿态数据，没有速度信息，所以使用前一个主题进行发布。要注意的是，APM中使用的是*FRD坐标系*（左边），而*MAVROS*使用的是*FLU坐标系*（右边），它内部会自动完成这两者的转化，因此导入数据时只要能保证数据是基于*FLU*的即可。如果使用了电子罗盘作为外部偏航角输入，则APM参考系变为*NED坐标系*具体细节参考：    
http://docs.px4.io/main/en/ros/external_position_estimation.html
>  

### PID参数
>1. 角度控制器。  
>2. 角速度控制器。   
>3. 垂直加速度控制器，垂直速度控制器，垂直位置控制器。  
>4. 水平位置控制器，水平速度控制器。  
>  

### 飞行数据
>1. 点击*飞行数据*，*数据闪存日志*，*通过MAVLINK下载闪存日志*把SD卡中的对应数据文件下载到本地。  
>     
>2. 点击*回顾日志*，选择对应日志文件后打开会出现数据图表。图表右侧中是记录下来的各项数据，勾选对应数据即可显示，例如勾选*ATT*中的*DesRoll*和*Roll*。  
>    
>>部分重要数据说明：   
>>ATT: 飞机三轴姿态，包含期望姿态与实际姿态。  
CTUN: 高度信息以及油门控制信息。  
IMU: 各个IMU的陀螺仪和加速度计数据。 
PSCX: 位置控制时，三轴方向上的期望位置，期望速度，期望加速度与实际位置，实际速度与实际加速度。  
RATE: 飞机三轴期望角速度与实际速度，垂直方向期望加速度与实际加速度。  
RCIN:  遥控器个通道输入。  
VIBE: 各个IMU的震动偏差值。  
VISP: 外部定位数据。  
XKF1: 外部定位数据与IMU融合后的位姿数据。  

### 配置参数（部分）
例举了部分重要配置参数及其简介，在后方括号中是默认配置文件中的值。  
>AHRS_EKF_TYPE: 传感器融合计算器，可选EKF2或者EKF3。（3）  
>AHRS_GPS_USE: 是否使用GPS。（0）  
>AHRS_ORIENTATION: IMU X轴朝向。（0）  
>ARMING_CHECK: 起飞前检查的数据。（386）  
>ATC: pid参数。  
>BATT_LOW_TIMER: 电池电压不足后多久出发动作。（5）  
>BATT_LOW_VOLT: 电池低电压触发值。（13.5）  
>BATT_MONITOR: 监控模式。（3）  
>BATT_VOLT_MULT: 电压系数，用于把读取到的信号值转化为真实电压数据。（10.88）  
>BATT_CURR_PIN: 飞控板型号以配置检测引脚。（3）  
>BATT_FS_CRT_ACT:  低电压触发后执行的动作。 （1）  
>BATT_FS_LOW_ACT:  低电压触发后执行的动作。 （1）   
>BRD_RTC_TYPES: 选择时钟信号源。（6）  
>BRD_TYPE: 飞控板型号。（2）  
>COMPASS_ENABLE: 是否激活罗盘。（0）  
>EK3_ACC_P_NSE: 加速度计信任权重，越大越不信任。（1）  
>EK3_ALT_M_NSE: 气压计信任权重，越大越不信任。（10）  
>EK3_BCN_M_NSE: Becon信任权重，越大越不信任。（10）  
>EK3_EAS_M_NSE: 空速计信任权重，越大越不信任。（5）   
>EK3_ENABLE: 启动EKF3。（1）  
>EK3_FLOW_M_NSE: 光流信任权重，越大越不信任。（1）  
>EK3_FLOW_USE: 使用光流。（0）  
>EK3_HGT_DELAY: 高度数据与IMU数据时间差。（150）  
>EK3_PRIMARY: 优先使用那个IMU。（1）  
>EK3_SRCX_POSXY: 水平位置数据来源。（6）    
>EK3_SRCX_POSZ: 垂直位置数据来源。（6）   
>EK3_SRCX_VELXY: 水平速度数据来源。（6）   
>EK3_SRCX_VELZ: 垂直速度数据来源。（6）   
>EK3_SRCX_YAW: 偏航角数据来源。（6）     
>FLTMODE_CH: 控制模式切换的通道。（5）    
>FLEMODEX: 不同数值对应的飞行模式。    
>RNGFNDX_TYPE: 接入的测距模块型号。（0）  
>RCX_OPTION: 该通道绑定的行为。  (RC7_OPTION:18)    
>SERIAL1_BAUD: 串口模特率。（921）    
>SERIAL1_PROTOCOL: 通信协议。（2）   
>SERIAL2_BAUD: 串口模特率。（921）    
>SERIAL2_PROTOCOL: 通信协议。（2）   
>VISO_TYPE: 外部定位数据类型。（2）    
>VISO_DELAY_MS: 外部定位数据延时。 （150）    
>VISO_ORIENT: 相机朝向。（0）    
>VISO_POS_M_NSE: 外部定位数据信任权重，越大越不信任。（0.1）  

## Q&A
---
### Jetson NX突然卡死
>有一种可能性是分配的swap空间太小，运行程序过程中把内存占满导致系统卡死，增加swap空间可解决该问题。  
1. `sudo fallocate 6G /swapfile`  
2. `sudo chmod 560 /swapfile`    
3. `sudo mkswap /swapfile`    
4. `sudo swapon /swapfile`   
5. `sudo cp /etc/fstab /etc/fstab.bak`  
6. `echo '/swapfile none swap sw 0 0' | sudo tee -a /etc/fstab`  

### 时间同步问题
>NX如果没有接入互联网，其系统时间与主机会不一致，会导致程序编译，文件同步等出问题，可使用 *chrony* 工具同步主机与NX的时间。  
>1. 在NX与主机都安装chrony： `sudo apt install chrony`   
>2. 在主机的 */etc/chrony/chrony.conf* 文件中添加 *allow 192.168.100.1/24*, 这个网段需要根据自己的配置进行设置。然后重启服务： `sudo systemctl restart chrony`  
>3. 如下图修改NX的 */etc/chrony/chrony.conf* 文件，server地址是主机的IP地址，然后重启服务： `sudo systemctl restart chrony`  
>   
>4. 在NX中执行 `chronyc waitsync`， 等待同步完成即可。  

### 手动定点模式水平方向持续漂移
>其中一个可能性是遥控的输入没有校准，导致水平方向持续输出杆量。可以通过查看飞行数据的*RCIN*第2，第4通道（pitch和roll对应的通道）确认是否如此。这种情况可以通过在MissionPlanner中校准遥控以及遥控器自身的校准解决。遥控器校准功能需要长按*menu*后按*page*进入第6页，按提示操作即可。   
>

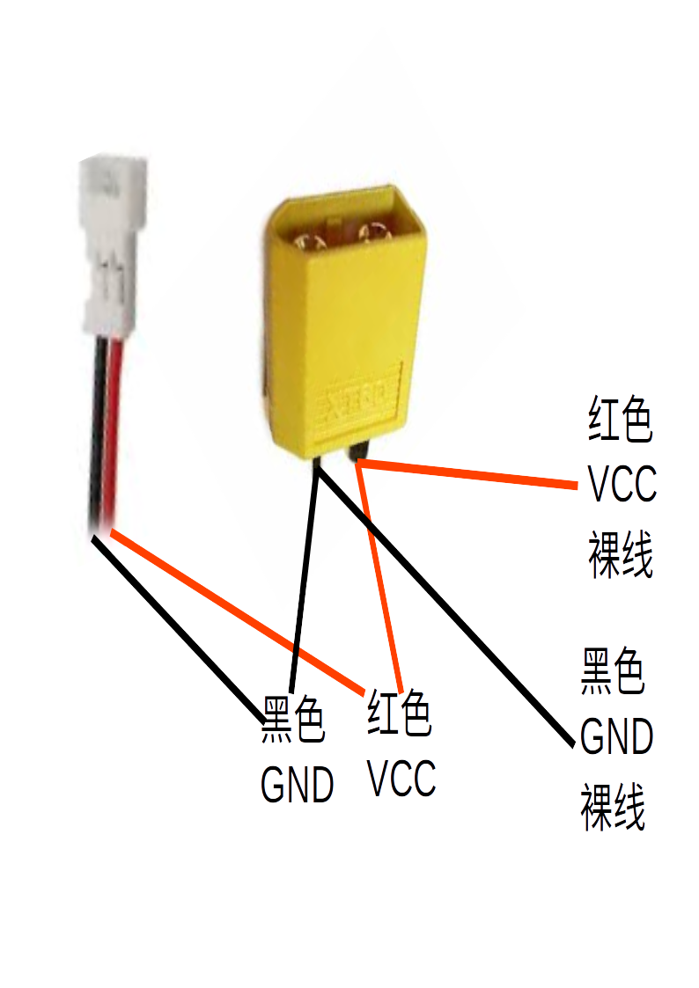
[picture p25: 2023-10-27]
docs/pics/风扇电池电源线.png

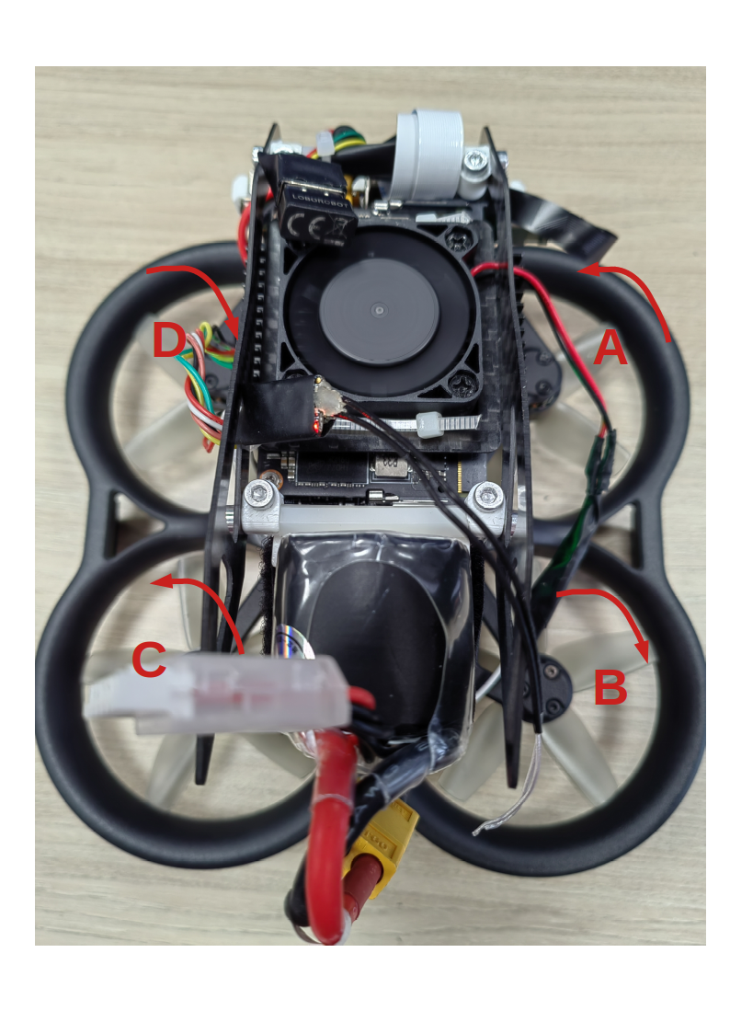
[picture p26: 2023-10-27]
docs/pics/qi5.tif

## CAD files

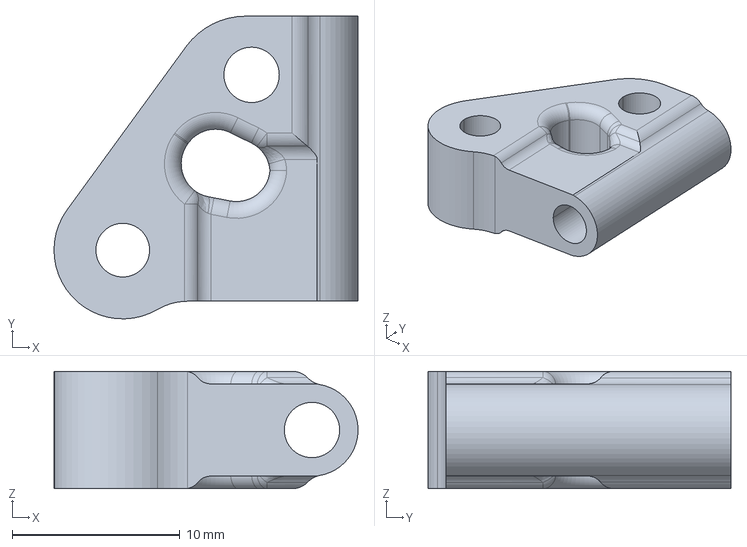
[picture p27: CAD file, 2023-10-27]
models/防护板固定支架_左.stp
18.1 x 18.0 x 7.00 mm

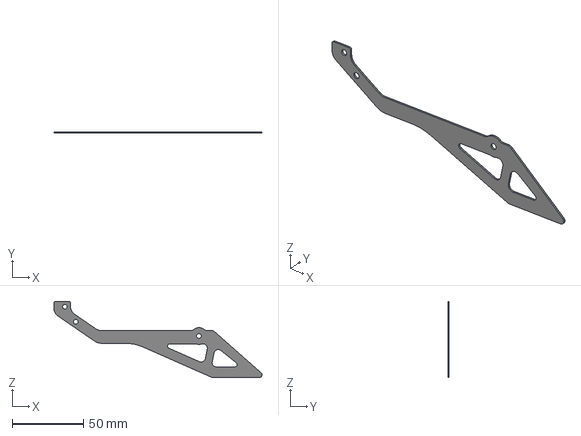
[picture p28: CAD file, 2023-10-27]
models/侧边防护板.stp
145.7 x 1.00 x 53.5 mm

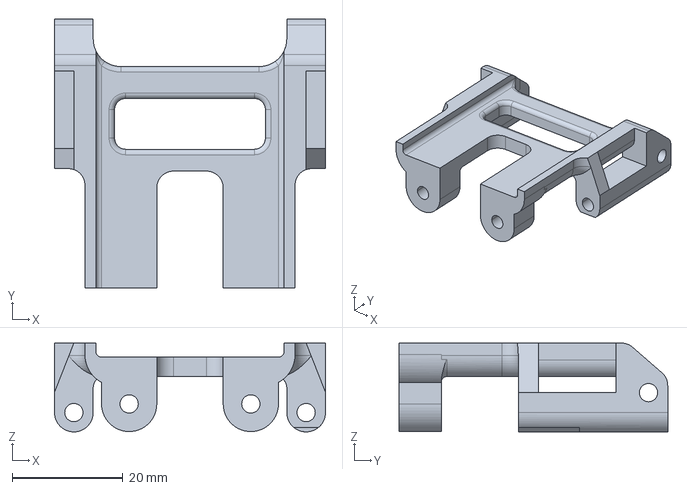
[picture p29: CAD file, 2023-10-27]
models/电池固定支架.stp
49.0 x 48.6 x 16.1 mm

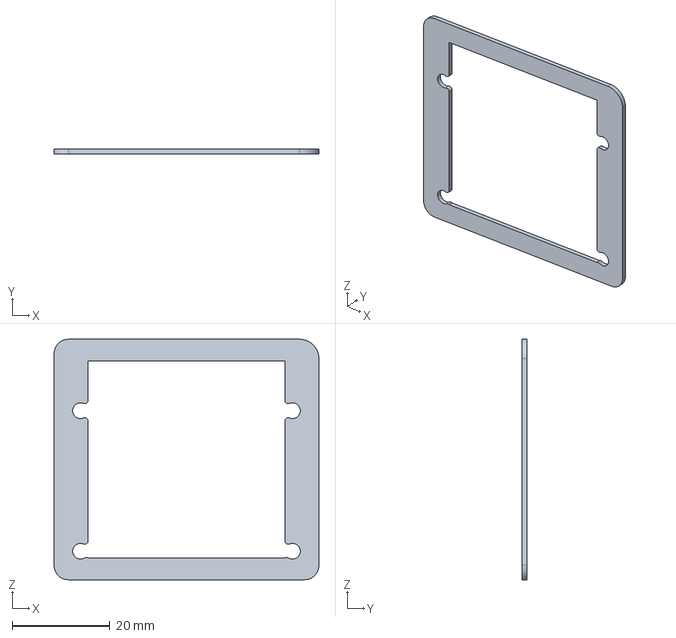
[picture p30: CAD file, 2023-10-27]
models/风扇固定板.stp
54.3 x 1.00 x 49.3 mm

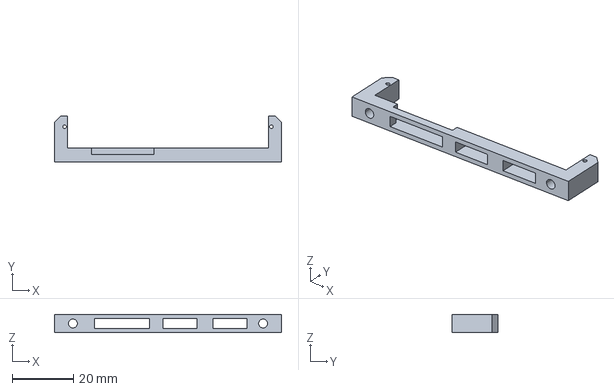
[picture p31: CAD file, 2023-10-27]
models/相机固定支架.stp
74.0 x 15.0 x 6.00 mm

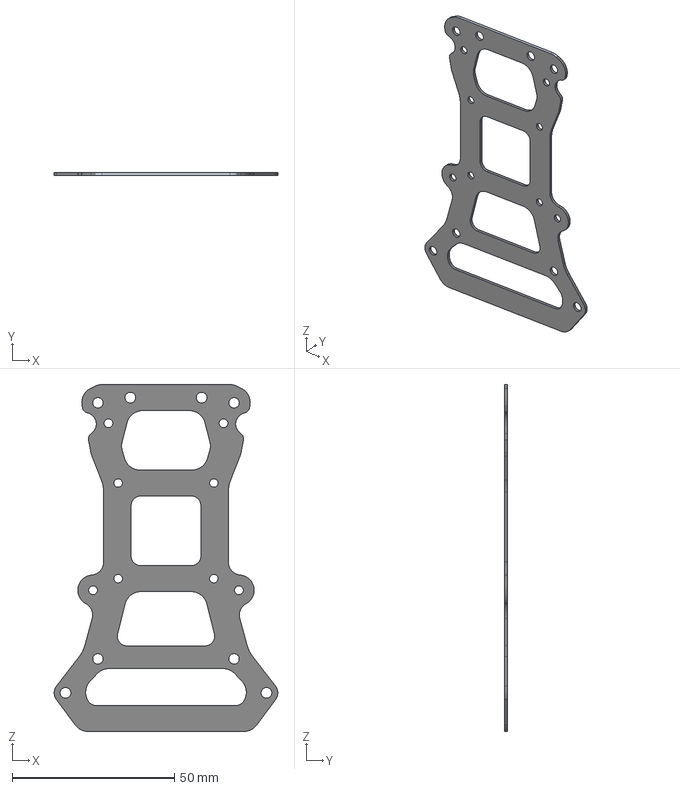
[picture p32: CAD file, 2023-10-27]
models/飞控固定板.stp
69.0 x 1.00 x 107.1 mm

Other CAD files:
models/防护板固定支架_右.stp

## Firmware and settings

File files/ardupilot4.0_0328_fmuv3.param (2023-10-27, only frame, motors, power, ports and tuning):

ATC_ANG_LIM_TC,1
ATC_ANG_PIT_P,11
ATC_ANG_RLL_P,10
ATC_ANG_YAW_P,15
ATC_ANGLE_BOOST,1
ATC_RAT_PIT_D,0.002
ATC_RAT_PIT_FF,0
ATC_RAT_PIT_FLTD,67
ATC_RAT_PIT_FLTE,0
ATC_RAT_PIT_FLTT,67
ATC_RAT_PIT_I,0.03
ATC_RAT_PIT_IMAX,0.5
ATC_RAT_PIT_P,0.225
ATC_RAT_PIT_SMAX,0
ATC_RAT_RLL_D,0.002
ATC_RAT_RLL_FF,0
ATC_RAT_RLL_FLTD,67
ATC_RAT_RLL_FLTE,0
ATC_RAT_RLL_FLTT,67
ATC_RAT_RLL_I,0.03
ATC_RAT_RLL_IMAX,0.5
ATC_RAT_RLL_P,0.2
ATC_RAT_RLL_SMAX,0
ATC_RAT_YAW_D,0.002
ATC_RAT_YAW_FF,0
ATC_RAT_YAW_FLTD,0
ATC_RAT_YAW_FLTE,2
ATC_RAT_YAW_FLTT,67
ATC_RAT_YAW_I,0.03
ATC_RAT_YAW_IMAX,0.5
ATC_RAT_YAW_P,0.5
ATC_RAT_YAW_SMAX,0
ATC_RATE_FF_ENAB,1
ATC_RATE_P_MAX,0
ATC_RATE_R_MAX,0
ATC_RATE_Y_MAX,0
BATT_AMP_OFFSET,0
BATT_AMP_PERVLT,17
BATT_ARM_MAH,0
BATT_ARM_VOLT,0
BATT_CAPACITY,3300
BATT_CRT_MAH,0
BATT_CRT_VOLT,0
BATT_CURR_PIN,3
BATT_FS_CRT_ACT,1
BATT_FS_LOW_ACT,1
BATT_FS_VOLTSRC,0
BATT_LOW_MAH,0
BATT_LOW_TIMER,5
BATT_LOW_VOLT,13.5
BATT_MONITOR,3
BATT_OPTIONS,0
BATT_SERIAL_NUM,-1
BATT_VLT_OFFSET,0
BATT_VOLT_MULT,10.88213
BATT_VOLT_PIN,2
BATT2_MONITOR,0
BATT3_MONITOR,0
BATT4_MONITOR,0
BATT5_MONITOR,0
BATT6_MONITOR,0
BATT7_MONITOR,0
BATT8_MONITOR,0
BATT9_MONITOR,0
FLTMODE_CH,5
FLTMODE1,5
FLTMODE2,0
FLTMODE3,0
FLTMODE4,2
FLTMODE5,0
FLTMODE6,0
FRAME_CLASS,1
FRAME_TYPE,1
INS_GYRO_FILTER,134
INS_HNTCH_ENABLE,0
MOT_BAT_CURR_MAX,0
MOT_BAT_CURR_TC,5
MOT_BAT_IDX,0
MOT_BAT_VOLT_MAX,16.8
MOT_BAT_VOLT_MIN,13.2
MOT_BOOST_SCALE,0
MOT_HOVER_LEARN,2
MOT_PWM_MAX,2000
MOT_PWM_MIN,1000
MOT_PWM_TYPE,6
MOT_SAFE_DISARM,0
MOT_SAFE_TIME,1
MOT_SLEW_DN_TIME,0
MOT_SLEW_UP_TIME,0
MOT_SPIN_ARM,0.07
MOT_SPIN_MAX,0.95
MOT_SPIN_MIN,0.07
MOT_SPOOL_TIME,0.5
MOT_THST_EXPO,0.45
MOT_THST_HOVER,0.2554513
MOT_YAW_HEADROOM,200
SERIAL0_BAUD,57
SERIAL0_PROTOCOL,2
SERIAL1_BAUD,921
SERIAL1_OPTIONS,0
SERIAL1_PROTOCOL,2
SERIAL2_BAUD,921
SERIAL2_OPTIONS,0
SERIAL2_PROTOCOL,2
SERIAL3_BAUD,921
SERIAL3_OPTIONS,0
SERIAL3_PROTOCOL,2
SERIAL4_BAUD,115
SERIAL4_OPTIONS,0
SERIAL4_PROTOCOL,9
SERIAL5_BAUD,57
SERIAL5_OPTIONS,0
SERIAL5_PROTOCOL,-1
SERVO1_FUNCTION,0
SERVO1_MAX,1900
SERVO1_MIN,1100
SERVO1_REVERSED,0
SERVO1_TRIM,1500
SERVO2_FUNCTION,0
SERVO2_MAX,1900
SERVO2_MIN,1100
SERVO2_REVERSED,0
SERVO2_TRIM,1500
SERVO3_FUNCTION,0
SERVO3_MAX,1900
SERVO3_MIN,1100
SERVO3_REVERSED,0
SERVO3_TRIM,1500
SERVO4_FUNCTION,0
SERVO4_MAX,1900
SERVO4_MIN,1100
SERVO4_REVERSED,0
SERVO4_TRIM,1500
SERVO5_FUNCTION,0
SERVO5_MAX,1900
SERVO5_MIN,1100
SERVO5_REVERSED,0
SERVO5_TRIM,1500
SERVO6_FUNCTION,0
SERVO6_MAX,1900
SERVO6_MIN,1100
SERVO6_REVERSED,0
SERVO6_TRIM,1500
SERVO7_FUNCTION,0
SERVO7_MAX,1900
SERVO7_MIN,1100
SERVO7_REVERSED,0
SERVO7_TRIM,1500
SERVO8_FUNCTION,0
SERVO8_MAX,1900
SERVO8_MIN,1100
SERVO8_REVERSED,0
SERVO8_TRIM,1500
SERVO9_FUNCTION,33
SERVO9_MAX,2000
SERVO9_MIN,1000
SERVO9_REVERSED,0
SERVO9_TRIM,1000

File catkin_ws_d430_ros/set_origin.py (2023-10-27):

#  Copyright © 2023 ROBOMASTER All Rights Reserved.
#  You may use, distribute and modify this code under the
#  terms of the MIT license, which unfortunately won't be
#  written for another century.

#!/usr/bin/env python

##
#
# Send SET_GPS_GLOBAL_ORIGIN and SET_HOME_POSITION messages
#
##

import rospy
from pymavlink.dialects.v10 import ardupilotmega as MAV_APM
from mavros.mavlink import convert_to_rosmsg
from mavros_msgs.msg import Mavlink

# Global position of the origin
lat = 425633500  # Terni
lon = 126432900  # Terni
alt = 163000 

class fifo(object):
    """ A simple buffer """
    def __init__(self):
        self.buf = []
    def write(self, data):
        self.buf += data
        return len(data)
    def read(self):
        return self.buf.pop(0)

def send_message(msg, mav, pub):
    """
    Send a mavlink message
    """
    msg.pack(mav)
    rosmsg = convert_to_rosmsg(msg)
    pub.publish(rosmsg)

    print("sent message %s" % msg)

def set_global_origin(mav, pub):
    """
    Send a mavlink SET_GPS_GLOBAL_ORIGIN message, which allows us
    to use local position information without a GPS.
    """
    target_system = mav.srcSystem
    #target_system = 0   # 0 --> broadcast to everyone
    lattitude = lat
    longitude = lon
    altitude = alt

    msg = MAV_APM.MAVLink_set_gps_global_origin_message(
            target_system,
            lattitude, 
            longitude,
            altitude)

    send_message(msg, mav, pub)

def set_home_position(mav, pub):
    """
    Send a mavlink SET_HOME_POSITION message, which should allow
    us to use local position information without a GPS
    """
    target_system = 0
    #target_system = 0  # broadcast to everyone

    lattitude = lat
    longitude = lon
    altitude = alt
    
    x = 0
    y = 0
    z = 0
    q = [1, 0, 0, 0]   # w x y z

    approach_x = 0
    approach_y = 0
    approach_z = 0

    msg = MAV_APM.MAVLink_set_home_position_message(
            target_system,
            lattitude,
            longitude,
            altitude,
            x,
            y,
            z,
            q,
            approach_x,
            approach_y,
            approach_z)

    send_message(msg, mav, pub)

if __name__=="__main__":
    try:
        rospy.init_node("origin_publisher")
        mavlink_pub = rospy.Publisher("/mavlink/to", Mavlink, queue_size=20)

        # Set up mavlink instance
        f = fifo()
        mav = MAV_APM.MAVLink(f, srcSystem=1, srcComponent=1)

        # wait to initialize
        while mavlink_pub.get_num_connections() <= 0:
            pass
   
        for _ in range(2):
            rospy.sleep(1)
            set_global_origin(mav, mavlink_pub)
            set_home_position(mav, mavlink_pub)
    except rospy.ROSInterruptException:
        pass

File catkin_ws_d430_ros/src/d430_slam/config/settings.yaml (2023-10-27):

#  Copyright © 2023 ROBOMASTER All Rights Reserved.
#  You may use, distribute and modify this code under the
#  terms of the MIT license, which unfortunately won't be
#  written for another century.

%YAML:1.0

#--------------------------------------------------------------------------------------------
# Camera Parameters. Adjust them!
#--------------------------------------------------------------------------------------------
File.version: "1.0"

Camera.type: "PinHole"



# Rectified Camera calibration and distortion parameters (OpenCV)
Camera1.fx: 382.328
Camera1.fy: 382.328
Camera1.cx: 319.108
Camera1.cy: 236.605

Camera2.fx: 382.328
Camera2.fy: 382.328
Camera2.cx: 319.108
Camera2.cy: 236.605


Camera1.k1: 0.0
Camera1.k2: 0.0
Camera1.k3: 0.0
Camera1.k4: 0.0
Camera1.p1: 0.0
Camera1.p2: 0.0

Camera2.k1: 0.0
Camera2.k2: 0.0
Camera2.k3: 0.0
Camera1.k4: 0.0
Camera2.p1: 0.0
Camera2.p2: 0.0

Stereo.T_c1_c2:
  rows: 4
  cols: 4
  dt: f
  data: [1.0, 0.0,0.0, 0.0500961,
         0.0,1.0,0.0, 0.0,
         0.0,0.0,1.0,0.0,
         0.0,0.0,0.0,1.0]

Stereo.b: 0.0500961



# Camera resolution
Camera.width: 640
Camera.height: 480

# Camera frames per second 
Camera.fps: 12

# Color order of the images (0: BGR, 1: RGB. It is ignored if images are grayscale)
Camera.RGB: 1

# Close/Far threshold. Baseline times.
Stereo.ThDepth: 100.0

# Lapping area between images (We must calculate)
Camera1.overlappingBegin: 0
Camera1.overlappingEnd: 639

Camera2.overlappingBegin: 0
Camera2.overlappingEnd: 639


#--------------------------------------------------------------------------------------------
# ORB Parameters
#--------------------------------------------------------------------------------------------
# ORB Extractor: Number of features per image
ORBextractor.nFeatures: 600 #1250

# ORB Extractor: Scale factor between levels in the scale pyramid 	
ORBextractor.scaleFactor: 1.2

# ORB Extractor: Number of levels in the scale pyramid	
ORBextractor.nLevels: 8

# ORB Extractor: Fast threshold
# Image is divided in a grid. At each cell FAST are extracted imposing a minimum response.
# Firstly we impose iniThFAST. If no corners are detected we impose a lower value minThFAST
# You can lower these values if your images have low contrast			
ORBextractor.iniThFAST: 20
ORBextractor.minThFAST: 7

#--------------------------------------------------------------------------------------------
# Viewer Parameters
#--------------------------------------------------------------------------------------------
Viewer.KeyFrameSize: 0.05
Viewer.KeyFrameLineWidth: 1.0
Viewer.GraphLineWidth: 0.9
Viewer.PointSize: 2.0
Viewer.CameraSize: 0.08
Viewer.CameraLineWidth: 3.0
Viewer.ViewpointX: 0.0
Viewer.ViewpointY: -0.7
Viewer.ViewpointZ: -3.5
Viewer.ViewpointF: 500.0
